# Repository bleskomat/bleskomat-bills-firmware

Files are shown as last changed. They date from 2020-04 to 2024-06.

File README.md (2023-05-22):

# bleskomat-bills-firmware

The Bleskomat Bills ATM is an offline Bitcoin Lightning Network ATM which accepts fiat bank notes and pays-out bitcoin. It's a great educational tool to give others a practical first experience with Bitcoin's Lightning Network.

You can buy the [Bleskomat Bills ATM](https://shop.bleskomat.com/product/bleskomat-bills-atm/) from the official Bleskomat shop. Alternatively, you can find all the components and equipment needed and build your own.

The Bleskomat Bills ATM must be paired with a server to facilitate Lightning Network payments on its behalf; see the options below:
* [Bleskomat Platform](https://platform.bleskomat.com) - non-custodial, requires a monthly subscription
* [bleskomat-server](https://github.com/bleskomat/bleskomat-server) - non-custodial, open-source, self-hosted solution
* [lnbits](https://github.com/lnbits/lnbits-legend) via the Bleskomat extension - open-source, self-hosted and possible to use custodial instances hosted by others; public instances of lnbits:
	* [legend.lnbits.com](https://legend.lnbits.com) - unstable, don't leave funds on this instance for very long

The rest of this document details the hardware and software requirements, how to build the hardware yourself, and instructions for compiling and uploading the firmware from source.

* [Requirements](#requirements)
	* [Hardware Requirements](#hardware-requirements)
	* [Software Requirements](#software-requirements)
* [Building the Hardware Device](#building-the-hardware-device)
	* [Prepare the breadboards](#prepare-the-breadboards)
		* [ESP32 devkit pinout](#esp32-devkit-pinout)
	* [Wiring the Power Supply](#wiring-the-power-supply)
		* [Optionally power the ESP32 devkit via 5V pin](#optionally-power-the-esp32-devkit-via-5v-pin)
	* [Wiring the E-Paper Module](#wiring-the-e-paper-module)
	* [Wiring the Button](#wiring-the-button)
	* [Wiring the Bill Acceptor](#wiring-the-bill-acceptor)
* [Installing Libraries and Dependencies](#installing-libraries-and-dependencies)
* [Compiling and Uploading to Device](#compiling-and-uploading-to-device)
* [Generate Font Header Files](#generate-font-header-files)
* [Configure Bill Acceptor](#configure-bill-acceptor)
* [Configuring the Device](#configuring-the-device)
	* [List of Configuration Options](#list-of-configuration-options)
	* [Browser-Based Configuration Tool](#browser-based-configuration-tool)
	* [Command-Line Configuration Tool](#command-line-configuration-tool)
	* [Hard-Coded Configuration](#hard-coded-configuration)
* [Changelog](#changelog)
* [Support](#support)
* [License](#license)
* [Trademark](#trademark)

## Requirements

This section includes information about the software and hardware requirements needed to build this project.

### Hardware Requirements

The following list includes all the parts needed to build the commercial Bleskomat ATM. The list includes direct links to suppliers of each part.

Basic components/equipment needed to build your own Bleskomat Bills ATM:
* 2 x breadboard (400-pin)
* Jumper wires (M-M)
* Jumper wires (M-F)
* ESP32 Devkit
* NV10 Bill Acceptor from Innovative Technologies
* WaveShare 4.2 inch E-Paper Module (b/w)
* Button
* 10k ohm resistor
* DC 5.5/2.1 mm DIP adapter
* 12V DC power adaptor (1.5A < 3A)
* Standard USB to micro USB cable

Optional components/equipment:
* Soldering iron
* 2.54 mm pins
* To power the ESP32 devkit from the 12V DC power supply:
	* XL4005 step-down converter
	* USB (F) adapter
	* Alternatively, you could use a USB car charger which includes both a step-down converter and USB (F) output

### Software Requirements

* [make](https://www.gnu.org/software/make/)
* [PlatformIO Core (CLI)](https://docs.platformio.org/en/latest/core/)
	* Version 6 or newer
	* Only the CLI ("Core") is required

## Building the Hardware Device

Before proceeding, be sure that you have all the project's [hardware requirements](#hardware-requirements).

### Prepare the breadboards

One breadboard is not large enough to accommodate all the pins of the ESP32 devkit due to the width of the devkit. This is why we recommend to connect two breadboards together.

Remove one of the power rails from one of the breadboards. Use the notches on the sides of the breadboards to connect them together length-wise.

Insert the ESP32 devkit into the pin holes of the new, combined breadboard.

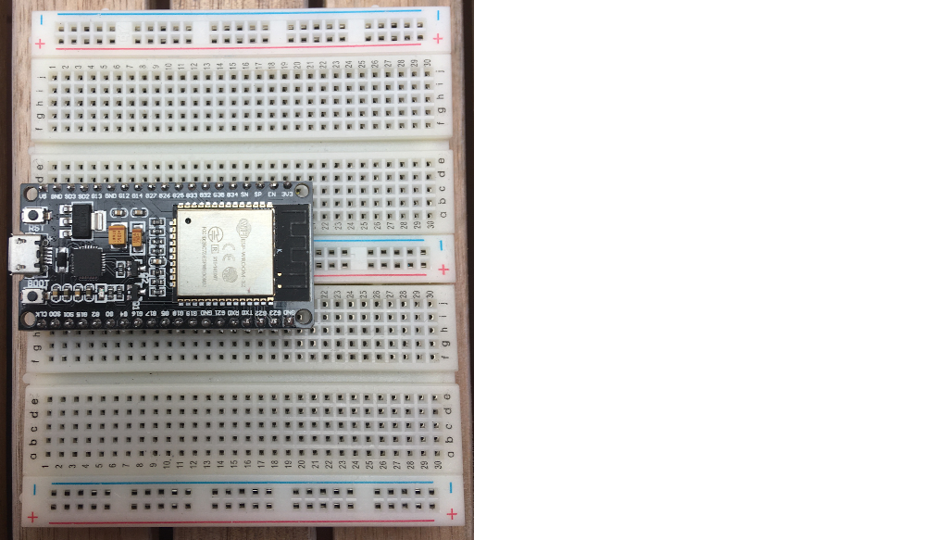
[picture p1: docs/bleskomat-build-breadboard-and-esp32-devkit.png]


Familiarize yourself with the ESP32 devkit's pinout reference below.

#### ESP32 devkit pinout

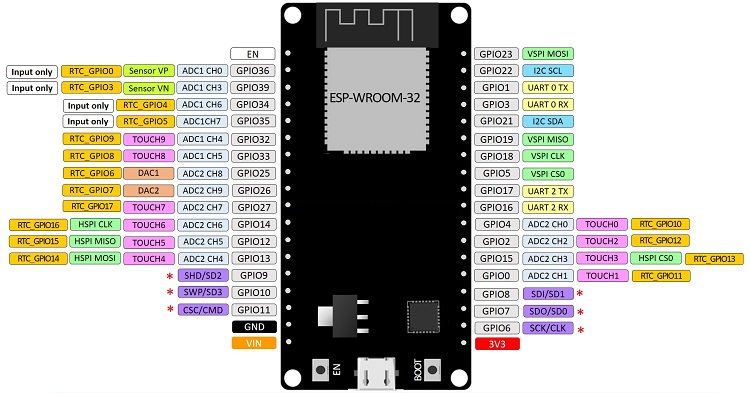
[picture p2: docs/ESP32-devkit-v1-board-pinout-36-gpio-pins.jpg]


### Wiring the Power Supply

The first step to building the device is wiring the power supply. If already plugged in, __unplug__ the 12V DC power supply now. Connect the DC 5.5/2.1 end of the power supply to the DIP adapter. The positive (+) pins should be the power pins and the negative (-) pins should be the ground. You can use your multimeter to check in case you want to be extra safe:
* Plug-in the power supply to electricity
* Turn on your multimeter and set it to measure voltage in the appropriate range (probably 20V)
* Touch the __red__ lead of your multimeter to one of the positive pins
* Touch the __black__ lead of your multimeter to one of the negative pins
* If you see a negative voltage reading, swap the leads between the two wires
* The pin touched by the __black__ lead is the ground ("GND")
* The pin touched by the __red__ lead is the hot wire ("DC12V")
* Unplug the power supply again

Use a pair of M-F jumper wires to connect the DC 5.5/2.1 DIP adapter to one of the breadboard's power rails. Negative to negative, positive to positive. This rail will be your 12V DC power (positive) and the common ground (negative).

#### Optionally power the ESP32 devkit via 5V pin

If you'd like to make your Bleskomat build a little bit more portable, you can power the ESP32 devkit via its 5V pin. To do this you will need the XL4005 (or equivalent) step-down converter and the USB (F) adapter. Note that powering the ESP32 devkit via its micro USB port requires a regulated voltage of approximately 5V.

It's also possible to use a USB car charger in case you have an extra one lying around.

Connect the step-down converter's input pins to the 12V DC power rail and common ground using (M-F) jumper wires. Use a multimeter to measure the voltage at the out pins. In the case of the XL4005, use a small screwdriver to turn the screw on the little blue box. Turning the screw counter clockwise should lower the voltage, turning it the opposite direction should increase the voltage. Once you have the voltage set to 5V, connect the out pins to the center power rails of the breadboard. This will be your 5V DC power rail.

Use a soldering iron to solder four 2.54 mm pins to the USB (F) DIP adapter. Insert the pins directly into the breadboard wherever you have space available. Using (M-M) jumper wires, connect the negative and positive pins of the USB (F) DIP adapter to the 5V DC power rail.

Connect the negative pin of the 5V DC power rail to the negative of the 12V DC power rail to ensure that they share a common ground. This is important because without a common ground shared between the coin acceptor and ESP32 devkit, the ESP32 will not receive a clean signal from the coin acceptor.

Use a standard USB to micro USB cable to connect the USB (F) DIP adapter to the ESP32 devkit.

There are other options when powering the ESP32 - e.g via the 3.3V pin or the 5V/VIN pin. You should __never__ power the ESP32 via more than one of these options at the same time. For example, do not power the ESP32 via its 3.3V pin while also connecting the ESP32 via USB to your computer. This can damage the ESP32 and possibly also your computer.

### Wiring the E-Paper Module

Connect the E-Paper display module to the ESP32 using the following table as a guide:

| ESP32 | E-Paper Display Module |
|---|---|
| D25 | BUSY |
| D26 | RST |
| D27 | DC |
| D15 | CS |
| D13 | CLK |
| D14 | DIN |
| GND | GND |
| 3.3V  | VCC |

Refer to the [ESP32 devkit pinout](#esp32-devkit-pinout) for help identifying the pins on your ESP32.

### Wiring the Button

Insert button pins into the breadboard wherever you have space available. Typically, its best to place the button at the center of a breadboard (over the gap).

Connect the button using the following table as a guide:

| ESP32 | Button |
|---|---|
| VIN (V5) | left pin  |
| GPIO33 | right pin |

Connect the right pin of the button to GND with a 10k ohm resistor.

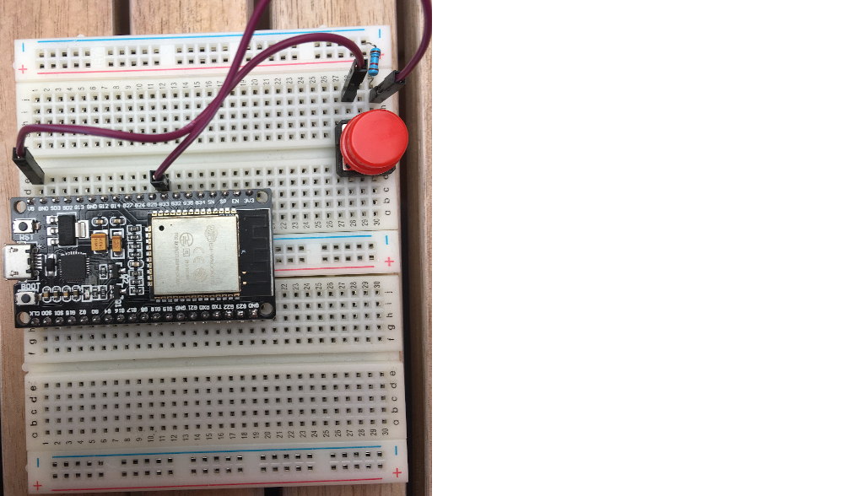
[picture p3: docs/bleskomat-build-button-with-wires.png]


Refer to the [ESP32 devkit pinout](#esp32-devkit-pinout) for help identifying the pins on your ESP32.

### Wiring the Bill Acceptor

This project supports the NV10 (USB+) and NV9 bill acceptors. The SIO protocol is used to communicate with the bill acceptor unit.

|  ESP32 | NV10/NV9 | Power Supply  |
|---|---|---|
| GPIO16 | 1 (Tx) | |
| GPIO17 | 5 (Rx) | |
| | 16 | - Ground |
| | 15 | + 12V DC |

Refer to the [ESP32 devkit pinout](#esp32-devkit-pinout) for help identifying the pins on your ESP32.

## Installing Libraries and Dependencies

Before proceeding, be sure that you have all the project's [software requirements](#software-requirements).

Use make to install libraries and dependencies for the device firmware:
```bash
make install
```
* The firmware's dependencies are defined in its platformio.ini file located at `./platformio.ini`

If while developing you need to install a new library for the device firmware, use the following as a guide:
```bash
platformio lib install LIBRARY_NAME[@VERSION]
```
You can find PlatformIO's libraries repository [here](https://platformio.org/lib).

## Compiling and Uploading to Device

To compile the firmware (without uploading to a device):
```bash
make compile
```

To compile and upload to your device:
```bash
make upload DEVICE=/dev/ttyUSB0
```
The device path for your operating system might be different. If you receive a "Permission denied" error about `/dev/ttyUSB0` then you will need to set permissions for that file on your system:
```bash
sudo chown $USER:$USER /dev/ttyUSB0
```

To open the serial monitor:
```bash
make monitor DEVICE=/dev/ttyUSB0
```
Again the device path here could be different for your operating system.

## Generate Font Header Files

Each font used to render text on the E-Paper display is loaded from a C-style header file. If you need to add another font, expand the character set of an existing font, or add more font sizes; you will need to generate new font header files.

Have otf2bdf utility installed on your system - available via `apt-get` or `apt` on Ubuntu - e.g `apt-get install otf2bdf`.

Manually build bdfconv from source which is included along with this repository:
```sh
make bdfconv
```
Generate fonts:
```sh
make fonts
```
To manually generate fonts:
```sh
./scripts/generate-font-header-files.sh "/path/to/font/file.ttf" 2 32-382 16,20,24,28,32,36,40,44,48
```
* `2` - this is the build mode
	* "Font build mode, 0: proportional, 1: common height, 2: monospace, 3: multiple of 8". Examples:
		* CheckbookLightning = 1
		* Courier Prime Code = 2
* `32-382` - this is the character range (e.g. first character = 32, last = 382). More characters = larger header files.
* `6,7,8,9,10,12,14,16,18,20,22,24,28` - comma-separated list of font sizes

Generated font files are written to the ./include/fonts/u8g2 directory.

## Configure Bill Acceptor

Please refer to the following user manuals for detailed instructions regarding how to configure the NV10 (USB+) bill acceptor:
* [NV10 User Manual](docs/NV10-User-Manual-v1.1.pdf)

## Configuring the Device

It is possible to configure the device via the following methods:
* [Browser-Based Configuration Tool](#browser-based-configuration-tool)
* [Command-Line Configuration Tool](#command-line-configuration-tool)
* [Hard-Coded Configuration](#hard-coded-configuration)

### List of Configuration Options

The following is a list of possible configuration options:
* `apiKey.id` - The API key ID of the device. This is needed by the server to verify signatures created by the device.
* `apiKey.key` - The API key secret that is used to generate signatures.
* `apiKey.encoding` - The explicit encoding of the API key secret. This can be "hex", "base64", or empty-string (e.g "") to mean no encoding. When generating a new API key on the server, it will store the encoding along with the ID and secret.
* `callbackUrl` - The LNURL server base URL plus endpoint path. Example:
	* `https://p.bleskomat.com/u`
* `shorten` - Whether or not to shorten the LNURL; see the [lnurl-node module](https://github.com/chill117/lnurl-node#signed-lnurls) for more details.
* `uriSchemaPrefix` - The URI schema prefix for LNURLs generated by the device. It has been discovered that some wallet apps mistakenly only support lowercase URI schema prefixes. Uppercase is better because when encoded as a QR code, the generated image is less complex and so easier to scan. Set this config to empty-string (e.g `uriSchemaPrefix=`) to not prepend any URI schema prefix.
* `fiatCurrency` - The fiat currency symbol for which the device is configured; see [ISO 4217](https://en.wikipedia.org/wiki/ISO_4217).
* `fiatPrecision` - The number of digits to the right of the decimal point when rendering fiat currency amounts.
* `billValues` - The value of bills for which the bill acceptor has been configured. Each value separated by a comma. Integers and floating point (decimal) values are accepted. Examples:
	* CZK: `100,200,500,1000,2000,5000`
	* EUR: `5,10,20,50,100,200,500`
* `billTxPin` - The GPIO connected to the NV10/NV9's Tx pin.
* `billRxPin` - The GPIO connected to the NV10/NV9's Rx pin.
* `billBaudRate` - The baud rate of the SIO protocol communication with the NV10/NV9. This value will be `300` or `9600`.
* `logLevel` - Possible values:
	* `trace` - everything
	* `debug`
	* `info` - default
	* `warn`
	* `error`
	* `none` - nothing
* `webUrl` - The base URL for the web platform. If non-empty, it will be the base URL for:
	* `/intro?id=API_KEY_ID` - URL shown as a QR code on the instructions screen.
* `platformSockUri` - If the device is connected to WiFi and this value is non-empty, a WebSocket connection will be created to the provided URI. Example values:
	* `wss://platform.bleskomat.com/device` -  Uses TLS encryption, must provide the intermediate CA certificate. This can be saved to the device's SPIFFS file system via the [/serial](https://platform.bleskomat.com/serial) tool.
	* `ws://platform.bleskomat.com/device` - Unencrypted WebSocket
* `platformCACert` - The PEM-encoded CA certificate for the platform. This is used to create a secure (TLS) connection to the platform.
* `onlineOnly` - If set to `1` or `true`, then the ATM will only be enabled when connected to the platform.

### Browser-Based Configuration Tool

The Bleskomat Platform provides a [browser-based configuration tool](https://platform.bleskomat.com/serial) to upload pre-built device firmware, view real-time log output, update device configurations, run JSON-RPC serial commands, and more.

### Command-Line Configuration Tool

It is also possible to use the [bleskomat-cli](https://github.com/bleskomat/bleskomat-cli) command-line utility to communicate with a Bleskomat hardware device via JSON-RPC over serial API. Please refer to that project's readme for installation and usage information.

### Hard-Coded Configuration

Hard-coded configurations can be set by modifying the source file [config.cpp](https://github.com/bleskomat/bleskomat-bills-firmware/blob/master/src/config.cpp#L201).

Each time you make changes to the hard-coded configurations, you will need to re-compile and flash the ESP32's firmware.

## Changelog

See [CHANGELOG.md](https://github.com/bleskomat/bleskomat-bills-firmware/blob/master/CHANGELOG.md)

## Support

Need some help? Join us in the official [Telegram group](https://t.me/bleskomat) or send us an email at [support@bleskomat.com](mailto:support@bleskomat.com) and we will try our best to respond in a reasonable time. If you have a feature request or bug to report, please [open an issue](https://github.com/bleskomat/bleskomat-bills-firmware/issues) in this project repository.

## License

The project is licensed under the [GNU General Public License v3 (GPL-3)](https://tldrlegal.com/license/gnu-general-public-license-v3-(gpl-3)):
> You may copy, distribute and modify the software as long as you track changes/dates in source files. Any modifications to or software including (via compiler) GPL-licensed code must also be made available under the GPL along with build & install instructions.

## Trademark

"Bleskomat" is a registered trademark. You are welcome to hack, fork, build, and use the source code and instructions found in this repository. However, the right to use the name "Bleskomat" with any commercial products or services is withheld and reserved for the trademark owner.

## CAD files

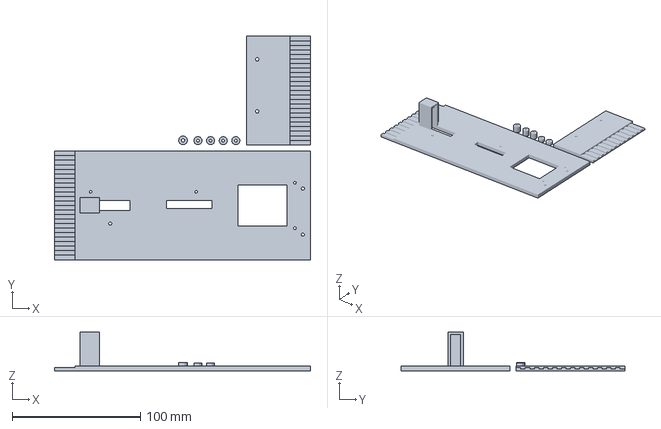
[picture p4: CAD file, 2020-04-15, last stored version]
3d-models/dell-pc-case/dell-pc-case--all.3mf
199.9 x 174.6 x 30.3 mm

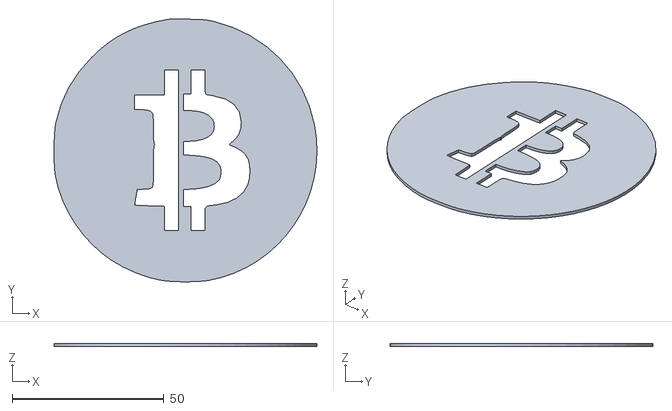
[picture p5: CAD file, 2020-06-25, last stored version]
assets/stencils/bitcoin-lightning/symbol.svg_1mm.stl
86.7 x 86.6 x 1.00

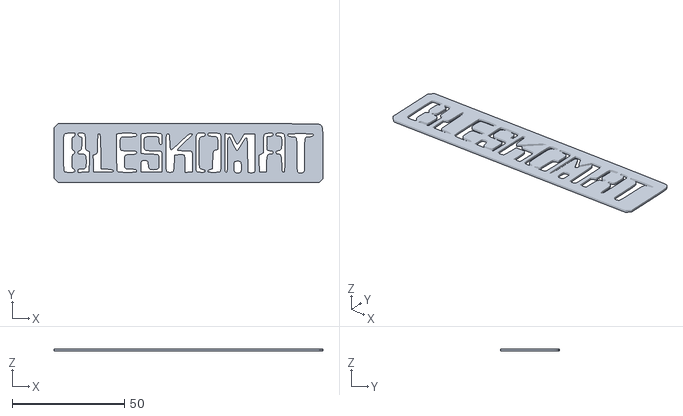
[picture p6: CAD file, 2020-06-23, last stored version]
assets/stencils/logo/stencil-120mm.svg_1mm.stl
120.0 x 26.3 x 1.00

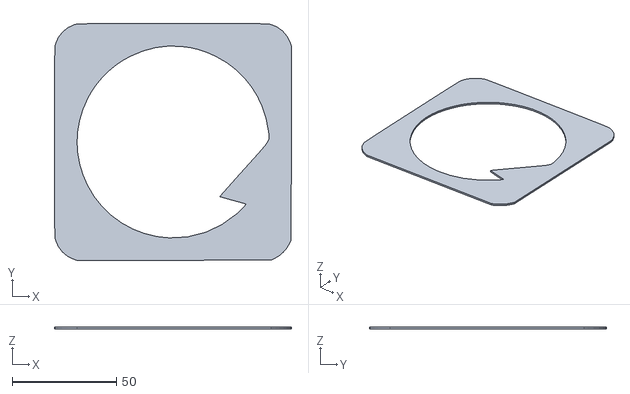
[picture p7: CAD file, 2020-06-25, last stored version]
assets/stencils/bitcoin-lightning/coin.svg_1mm.stl
113.9 x 113.9 x 1.00

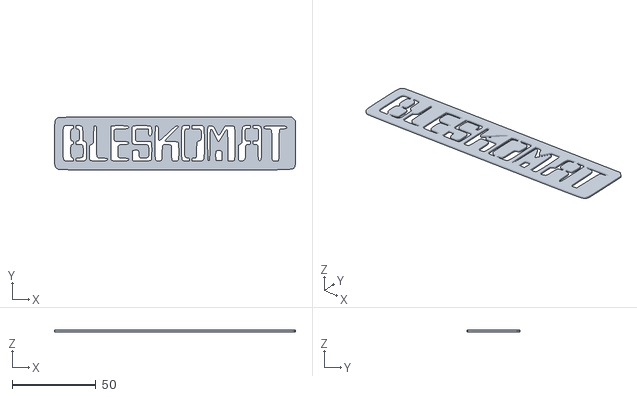
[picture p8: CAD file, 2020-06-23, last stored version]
assets/stencils/logo/stencil-144mm.svg_1mm.stl
143.5 x 31.5 x 1.00

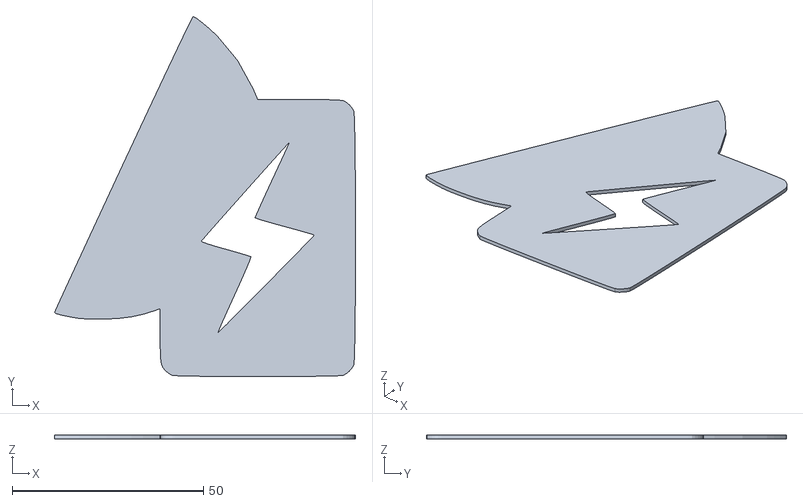
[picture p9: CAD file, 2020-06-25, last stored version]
assets/stencils/bitcoin-lightning/lightning.svg_1mm.stl
78.7 x 94.1 x 1.00

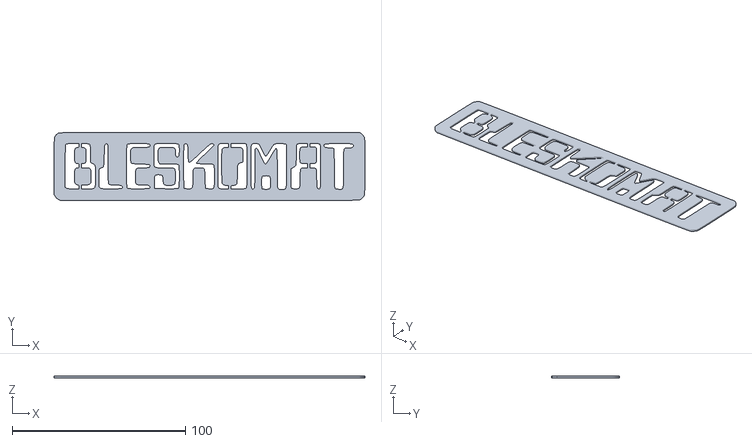
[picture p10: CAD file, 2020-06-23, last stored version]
assets/stencils/logo/stencil-180mm.svg_1mm.stl
179.5 x 39.3 x 1.00

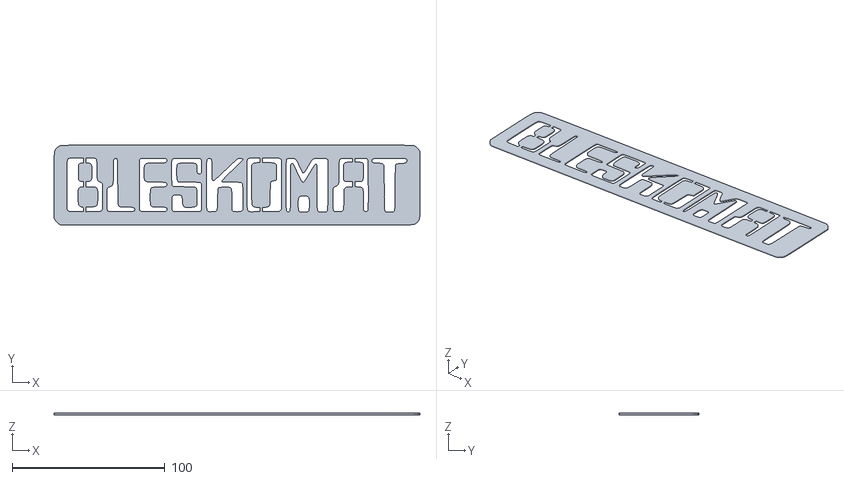
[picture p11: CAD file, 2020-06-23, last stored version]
assets/stencils/logo/stencil-240mm.svg_1mm.stl
240.0 x 52.5 x 1.00

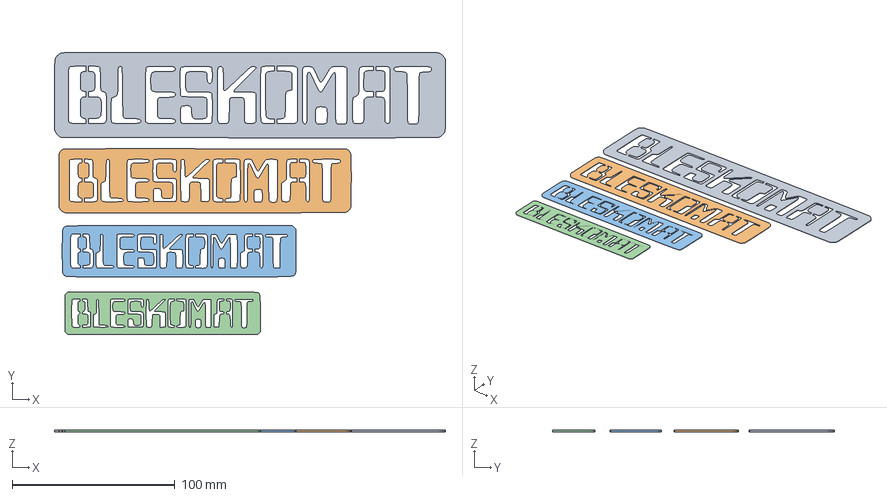
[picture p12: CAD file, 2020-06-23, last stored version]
assets/stencils/logo/stencil-120-240mm.svg_1mm.3mf
240.0 x 173.3 x 1.00 mm
stencil-240mm.svg_1mm.stl
stencil-180mm.svg_1mm.stl
stencil-144mm.svg_1mm.stl
stencil-120mm.svg_1mm.stl

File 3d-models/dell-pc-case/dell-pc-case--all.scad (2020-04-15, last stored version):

spaceBetweenPrintedParts=5;

plateWidth=84.8;
plateHeight=250;
plateThickness=4;

screwTypeOneDiameter=3;
screwTypeOneRadius=screwTypeOneDiameter / 2;
screwTypeTwoDiameter=2.5;
screwTypeTwoRadius=screwTypeTwoDiameter / 2;

// Mounts for parts (e.g screen and coin acceptor):
partMountWallThickness=2;
screenMountHeight=3.2;
coinAcceptorLeftMountHeight=6.1;
coinAcceptorRightMountHeight=6.4;

screwTopSpaceBetween=33;
screwTopLeftPosX=24.7 + screwTypeOneRadius;
screwTopLeftPosY=4.45 + screwTypeOneRadius;
screwTopRightPosX=screwTopLeftPosX + screwTypeOneRadius + screwTopSpaceBetween + screwTypeOneRadius;
screwTopRightPosY=screwTopLeftPosY;

screenMarginTop=10;
screenWidth=32;
screenHeight=38.35;
screenPosX=(plateWidth - screenWidth) / 2;
screenPosY=screwTopLeftPosY + screwTypeTwoDiameter + screenMarginTop;
screenScrewTopLeftPosX=(0.5 + screwTypeTwoRadius) * -1;
screenScrewTopLeftPosY=(5 + screwTypeTwoRadius) * -1;
screenScrewTopRightPosX=screenWidth + 0.5 + screwTypeTwoRadius;
screenScrewTopRightPosY=screenScrewTopLeftPosY;
screenMarginBottom=16;

coinAcceptorMarginTop=4;
coinInsertOutputGap=28.5;
coinOutputWidth=8.1;
coinOutputHeight=36.8;
coinOutputPosX=(plateWidth - coinOutputWidth) / 2;

coinInsertWidth=6.45;
coinInsertHeight=35.85;
coinInsertPosX=coinOutputPosX;
coinInsertPosY=screenPosY + screenHeight + screenMarginBottom + coinAcceptorMarginTop;
coinOutputPosY=coinInsertPosY + coinInsertHeight + coinInsertOutputGap;
coinOutputMarginBottom=22;

toothWidth=plateWidth / floor(plateWidth / 3.5);
toothHeight=16;
topPlateHeight=coinOutputHeight + coinOutputPosY + coinOutputMarginBottom;
topPlatePosX=0;
topPlatePosY=0;
topPlateTeethPosX=topPlatePosX;
topPlateTeethPosY=(topPlatePosY + topPlateHeight) - toothHeight;

bottomPlateHeight=plateHeight - topPlateHeight;
bottomPlatePosX=topPlatePosX + plateWidth + spaceBetweenPrintedParts;
bottomPlatePosY=topPlatePosY;
bottomPlateTeethPosX=0;
bottomPlateTeethPosY=0;

screwBottomSpaceBetween=36.2;
screwBottomLeftPosX=24.65 + screwTypeOneRadius;
screwBottomLeftPosY=bottomPlateHeight - (screwTypeOneDiameter + screwTypeOneRadius + 3.9);
screwBottomRightPosX=screwBottomLeftPosX + screwTypeOneDiameter + screwBottomSpaceBetween + screwTypeOneRadius;
screwBottomRightPosY=screwBottomLeftPosY;

coinAcceptorScrewTopPosX=(7.85 + screwTypeTwoRadius) * -1;
coinAcceptorScrewTopPosY=11.25 + screwTypeTwoRadius;
coinAcceptorScrewBottomPosX=(7.85 + screwTypeTwoRadius) * -1;
coinAcceptorScrewBottomPosY=coinOutputHeight - (5 + screwTypeTwoRadius);
coinAcceptorScrewRightPosX=(14 + screwTypeTwoRadius);
coinAcceptorScrewRightPosY=14 + screwTypeTwoRadius;

maxExpectedCoinDiameter=26.3;
maxExpectedCoinRadius=maxExpectedCoinDiameter / 2;
coinCatchWallThickness=2;
coinCatchWidth=coinOutputWidth + (coinCatchWallThickness * 2);
coinCatchHeight=maxExpectedCoinRadius + coinCatchWallThickness;
coinCatchDepth=maxExpectedCoinDiameter + coinCatchWallThickness;
coinCatchPosX=coinOutputPosX - coinCatchWallThickness;
coinCatchPosY=(coinOutputPosY + coinOutputHeight + coinCatchWallThickness) - coinCatchHeight;
coinCatchPosZ=plateThickness + (coinCatchWallThickness * -1);

// plate (top)
translate([topPlatePosX, topPlatePosY]) {
    union() {
        difference() {
            // plate
            cube([
                plateWidth,
                topPlateHeight,
                plateThickness
            ]);
            // screw (top-left)
            translate([
                // Invert x-coordinate:
                plateWidth - (screwTopLeftPosX + screwTypeOneDiameter),
                screwTopLeftPosY
            ]) {
                cylinder(
                    h=plateThickness,
                    r=screwTypeOneRadius
                );
            }
            // screw (top-right)
            translate([
                plateWidth - (screwTopRightPosX + screwTypeOneDiameter),
                screwTopRightPosY
            ]) {
                cylinder(
                    h=plateThickness,
                    r=screwTypeOneRadius
                );
            }
            // screen
            translate([screenPosX, screenPosY]) {
                cube([
                    screenWidth,
                    screenHeight,
                    plateThickness
                ]);
                // screen screw (top-left)
                translate([
                    screenScrewTopLeftPosX,
                    screenScrewTopLeftPosY
                ]) {
                    cylinder(
                        h=plateThickness,
                        r=screwTypeTwoRadius
                    );
                }
                // screen screw (top-right)
                translate([
                    screenScrewTopRightPosX,
                    screenScrewTopRightPosY
                ]) {
                    cylinder(
                        h=plateThickness,
                        r=screwTypeTwoRadius
                    );
                }
            }
            // coin insert
            translate([
                // Invert x-coordinate:
                plateWidth - (coinInsertPosX + coinInsertWidth),
                coinInsertPosY
            ]) {
                cube([
                    coinInsertWidth,
                    coinInsertHeight,
                    plateThickness
                ]);
                // screw (top)
                translate([
                    // Invert x-coordinate:
                    coinInsertWidth - (coinAcceptorScrewTopPosX + screwTypeTwoDiameter),
                    coinAcceptorScrewTopPosY
                ]) {
                    cylinder(
                        h=plateThickness,
                        r=screwTypeTwoRadius
                    );
                }
            }
            // coin output
            translate([coinOutputPosX, coinOutputPosY]) {
                cube([
                    coinOutputWidth,
                    coinOutputHeight,
                    plateThickness
                ]);
                // screw (bottom)
                translate([
                    // Invert x-coordinate:
                    coinOutputWidth - (coinAcceptorScrewBottomPosX + screwTypeTwoDiameter),
                    coinAcceptorScrewBottomPosY
                ]) {
                    cylinder(
                        h=plateThickness,
                        r=screwTypeTwoRadius
                    );
                }
                // screw (right)
                translate([
                    // Invert x-coordinate:
                    coinOutputWidth - (coinAcceptorScrewRightPosX + screwTypeOneDiameter),
                    coinAcceptorScrewRightPosY
                ]) {
                    cylinder(
                        h=plateThickness,
                        r=screwTypeOneRadius
                    );
                }
            }
            // teeth
            translate([
                topPlateTeethPosX,
                topPlateTeethPosY,
                plateThickness * (2/3)
            ]) {
                cube([
                    plateWidth,
                    toothHeight,
                    (plateThickness / 3) + 0.1
                ]);
                translate([0, 0, plateThickness / -3]) {
                    for (offsetX=[toothWidth : toothWidth * 2 : plateWidth]) {
                        translate([offsetX, 0]) {
                            cube([
                                toothWidth,
                                toothHeight,
                                (plateThickness / 3) + 0.1
                            ]);
                        }
                    }
                }
            }
        }
        // coin output catch
        difference() {
            translate([
                coinCatchPosX,
                coinCatchPosY,
                coinCatchPosZ
            ]) {
                cube([
                    coinCatchWidth,
                    coinCatchHeight,
                    coinCatchDepth
                ]);
            }
            translate([
                coinCatchPosX + coinCatchWallThickness,
                coinCatchPosY - coinCatchWallThickness,
                coinCatchPosZ - coinCatchWallThickness
            ]) {
                cube([
                    coinCatchWidth - (coinCatchWallThickness * 2),
                    coinCatchHeight,
                    coinCatchDepth
                ]);
            }
        }
    }
}
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

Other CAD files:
3d-models/case/bleskomat-prototype-case-v1.dxf
assets/case/bleskomat-prototype-case-v1.dxf
3d-models/dell-pc-case/dell-pc-case--all.stl
assets/dell-pc-case/dell-pc-case--all.stl

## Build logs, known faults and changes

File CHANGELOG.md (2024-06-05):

# Changelog

* v1.6.1:
	* Fix JSON-RPC getconfig when called with empty array should return all configurations
* v1.6.0:
	* Bluetooth JSON-RPC interface enabled when button pressed at boot
	* Wait for JSON-RPC serial interface to time-out before initializing e-paper, bill acceptor
* v1.5.0:
	* Update splash screen
	* Ping, reconnect to NV10 bill acceptor via serial
	* Fixup font rendering
	* Fix locale strings
	* Remove SD card related code
	* Cache state to be restored when device restarts in case of a crash, power loss, etc.
	* Add hardware build instructions
* v1.3.4:
	* Better initialization state handling
* v1.3.3:
	* Fix getInt/Short/Float config value when set to empty-string
* v1.3.2:
	* Added spiffsFormatted config flag
	* Return spiffsInitialized flag in getinfo JSON-RPC command
	* Send response for restart JSON-RPC command
* v1.3.1:
	* Fix randomly failing platform WebSocket connection
* v1.3.0:
	* Added "onlineOnly" configuration option
	* Fixed TLS connection problems
		* "platformCACert" configuration option can contain the CA cert for TLS
	* Improved logging
	* Simplify network/platform.cpp and SD card usage
	* Use SPIFFS file system to store logs
	* JSON-RPC via serial - echo, getconfig, setconfig, getlogs, deletelogs, spiffs_reformat, restart
	* Button delay to fix issue re: accidental clearing of QR code
	* Move bill/coin/button build flags to configuration options
	* Fix excessive memory usage (RAM) by i18n/locale
* v1.2.0:
	* Tagged release version

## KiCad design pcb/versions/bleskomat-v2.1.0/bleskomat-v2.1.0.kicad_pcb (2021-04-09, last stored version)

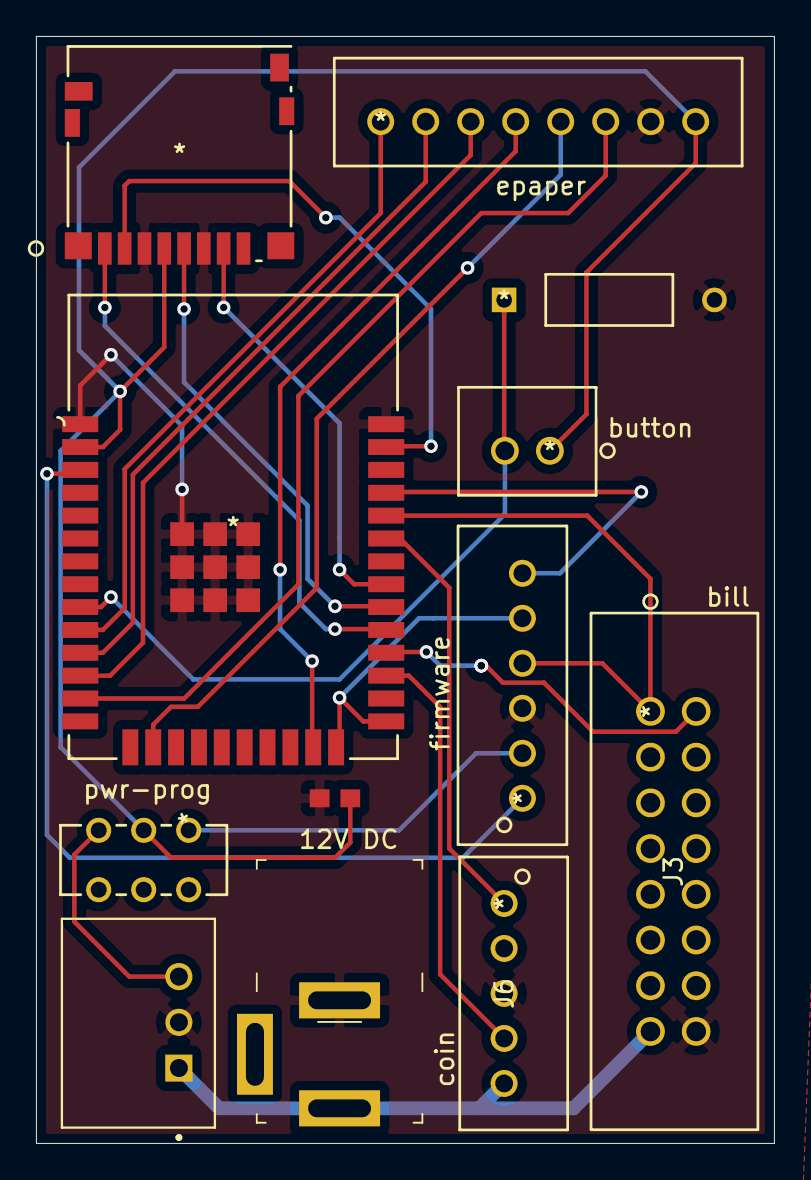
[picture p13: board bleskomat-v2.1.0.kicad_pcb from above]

Board: 2 copper layers, 41.0 x 61.5 mm, 12 parts (0 on the bottom side), 23 nets.

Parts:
12V DC: 12V-SOCKET; Barrel_Jack_5.5mmODx2.1mmID_PJ-202A
D1: LED-LTST-C194TBKT; 0603
J1: firmware; B6B-XH-ALFSN
J2: epaper; B8B-XH-A LFSN
J3: bill; 30316-6002HB
J4: button; B2B-XH-ALFSN
J5: SD_CARD; DM3D-SF
J6: coin; B5B-XH-A LFSN
PS1: step-down-R-78E3.3-1.0; CONV_R-78E3.3-1.0
R1: R 10K; CFR-25JB-52-10K
U1: ESP32-WROOM-32_8MB; ESP32-WROOM-32 8MB
U2: switch power JS202011CQN; JS202011CQN

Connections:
GND: 12V DC.2, D1.1, J1.3, J2.7, J3.16, J5.3, J5.6, J6.3, PS1.2, R1.2, U1.1, U1.38, U1.39, U1.40, U1.41, U1.42, U1.43, U1.44, U1.45, U1.46, U1.47
unnamed: D1.2, J2.8, J4.1, J5.4, U1.2, U2.2
unnamed: J1.1, U1.3
unnamed: J1.2, U2.1
unnamed: J1.4, J3.1, U1.34
unnamed: J1.5, U1.24, U1.25
unnamed: J1.6, U1.35
unnamed: J2.1, U1.10
unnamed: J2.2, U1.11
unnamed: J2.3, U1.12
unnamed: J2.4, U1.23
unnamed: J2.5, U1.16
unnamed: J2.6, U1.13
unnamed: J3.2, U1.28
unnamed: 12V DC.1, J3.15, J6.5, PS1.1
unnamed: J4.2, R1.1, U1.9
unnamed: J5.1, U1.29
unnamed: J5.2, U1.37
unnamed: J5.5, U1.30
unnamed: J5.7, U1.31
unnamed: J6.1, U1.33
unnamed: J6.4, U1.27
unnamed: PS1.3, U2.3

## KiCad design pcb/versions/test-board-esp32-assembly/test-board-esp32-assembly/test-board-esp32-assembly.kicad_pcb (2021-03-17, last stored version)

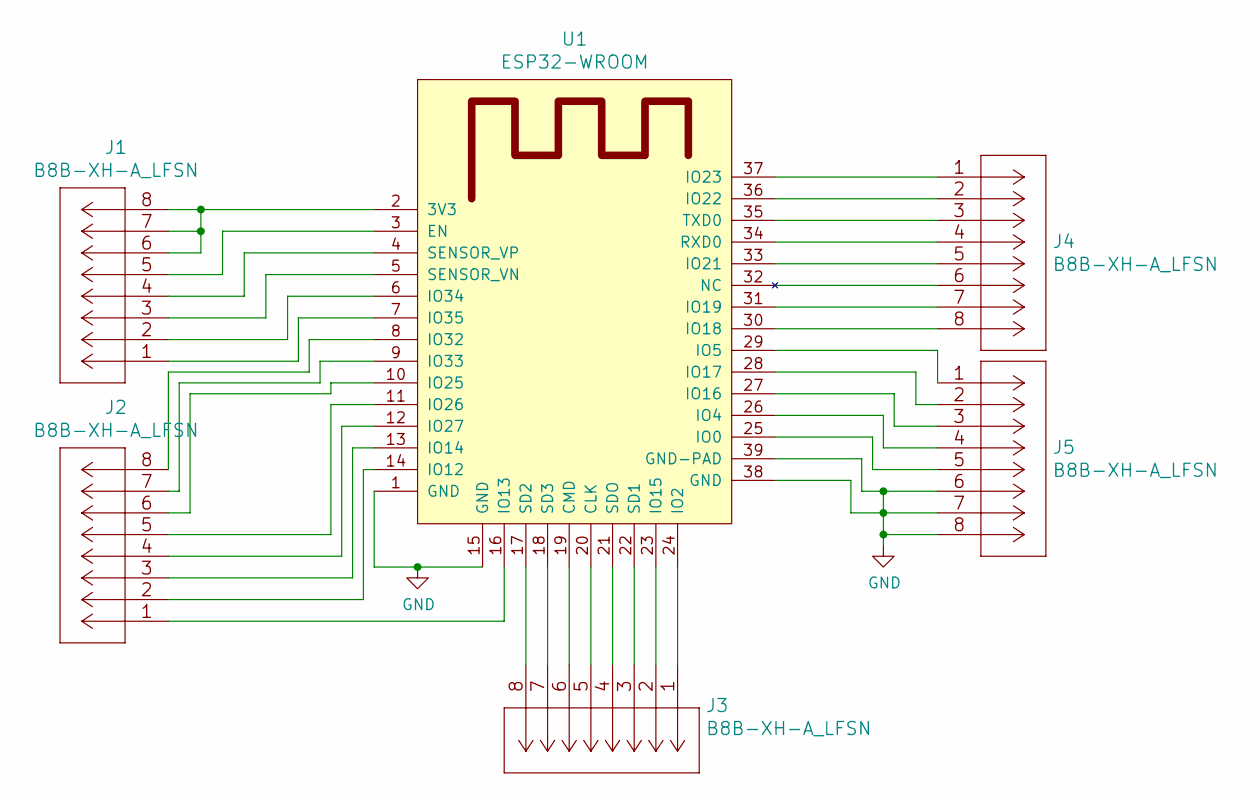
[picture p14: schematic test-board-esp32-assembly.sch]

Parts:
J1, J2, J3, J4, J5: B8B-XH-A_LFSN; B8B-XH-A LFSN
U1: ESP32-WROOM

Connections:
GND: J5.6, J5.7, J5.8, U1.1 (GND), U1.15 (GND), U1.38 (GND), U1.39 (GND-PAD)
unnamed: J1.1, U1.7 (IO35)
unnamed: J1.2, U1.6 (IO34)
unnamed: J1.3, U1.5 (SENSOR_VN)
unnamed: J1.4, U1.4 (SENSOR_VP)
unnamed: J1.5, U1.3 (EN)
unnamed: J1.6, J1.7, J1.8, U1.2 (3V3)
unnamed: J2.1, U1.16 (IO13)
unnamed: J2.2, U1.14 (IO12)
unnamed: J2.3, U1.13 (IO14)
unnamed: J2.4, U1.12 (IO27)
unnamed: J2.5, U1.11 (IO26)
unnamed: J2.6, U1.10 (IO25)
unnamed: J2.7, U1.9 (IO33)
unnamed: J2.8, U1.8 (IO32)
unnamed: J3.1, U1.24 (IO2)
unnamed: J3.2, U1.23 (IO15)
unnamed: J3.3, U1.22 (SD1)
unnamed: J3.4, U1.21 (SDO)
unnamed: J3.5, U1.20 (CLK)
unnamed: J3.6, U1.19 (CMD)
unnamed: J3.7, U1.18 (SD3)
unnamed: J3.8, U1.17 (SD2)
unnamed: J4.1, U1.37 (IO23)
unnamed: J4.2, U1.36 (IO22)
unnamed: J4.3, U1.35 (TXD0)
unnamed: J4.4, U1.34 (RXD0)
unnamed: J4.5, U1.33 (IO21)
unnamed: J4.6, U1.32 (NC)
unnamed: J4.7, U1.31 (IO19)
unnamed: J4.8, U1.30 (IO18)
unnamed: J5.1, U1.29 (IO5)
unnamed: J5.2, U1.28 (IO17)
unnamed: J5.3, U1.27 (IO16)
unnamed: J5.4, U1.26 (IO4)
unnamed: J5.5, U1.25 (IO0)

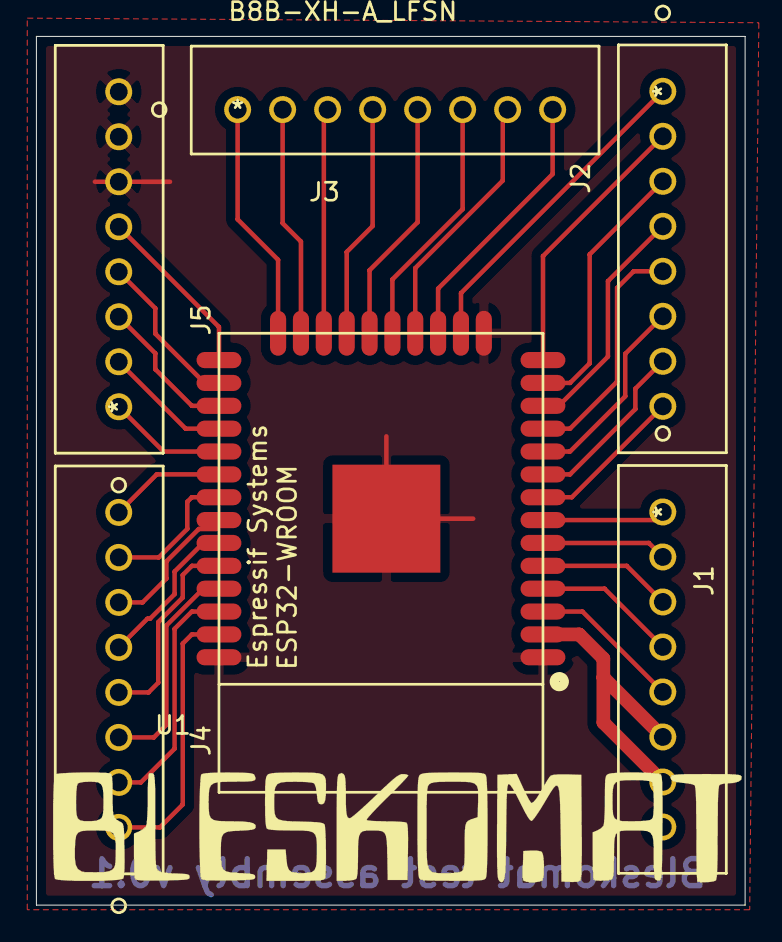
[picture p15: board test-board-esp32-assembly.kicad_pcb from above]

Board: 2 copper layers, 39.4 x 48.3 mm, 6 parts (0 on the bottom side), 36 nets.

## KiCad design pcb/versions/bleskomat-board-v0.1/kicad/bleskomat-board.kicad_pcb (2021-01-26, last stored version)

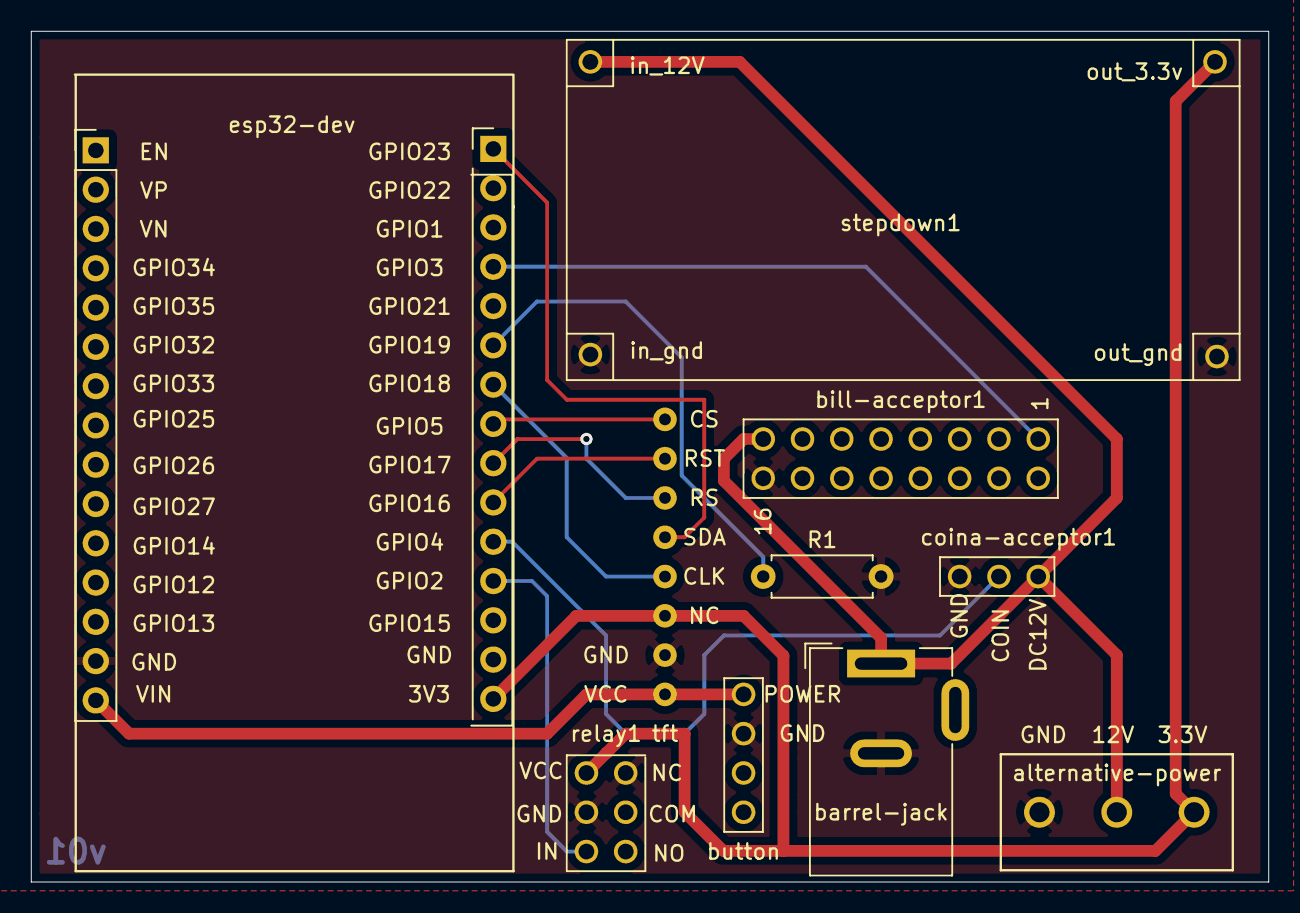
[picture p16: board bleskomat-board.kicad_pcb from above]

Board: 2 copper layers, 80.0 x 55.0 mm, 10 parts (0 on the bottom side), 13 nets.

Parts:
R1: 10k; R_Axial_DIN0207_L6.3mm_D2.5mm_P7.62mm_Horizontal
alternative-power: Screw_Terminal_01x03; TerminalBlock_5mm
barrel-jack: 12V-SOCKET; BarrelJack_Wuerth_6941xx301002
bill-acceptor1: billacceptor-connector
button: button; button-connector
coina-acceptor1: coinacceptor-connector
esp32-dev: esp32; ESP32_Devkit_DOIT_V2
relay1: relay-connector; relay-temporary-connector
stepdown1: stepdown-connector; stepdown
tft: tft-connector

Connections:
GND: R1.2, alternative-power.1, barrel-jack.2, bill-acceptor1.16, button.2, coina-acceptor1.3, esp32-dev.14, relay1.3, relay1.5, stepdown1.1, stepdown1.3, tft.7
unnamed: alternative-power.2, barrel-jack.1, bill-acceptor1.15, coina-acceptor1.1, stepdown1.2
unnamed: alternative-power.3, esp32-dev.16, relay1.6, stepdown1.4, tft.6
unnamed: R1.1, esp32-dev.25
unnamed: button.1, esp32-dev.15, tft.8
unnamed: esp32-dev.19, relay1.4
unnamed: coina-acceptor1.2, esp32-dev.20
unnamed: esp32-dev.21, tft.2
unnamed: esp32-dev.22, tft.3
unnamed: esp32-dev.23, tft.1
unnamed: esp32-dev.24, tft.5
unnamed: bill-acceptor1.1, esp32-dev.27
unnamed: esp32-dev.30, tft.4

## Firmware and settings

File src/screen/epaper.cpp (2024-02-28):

#include "screen/epaper.h"

//
//  Using GxEPD2 library:
//  	https://github.com/ZinggJM/GxEPD2
//  Which builds on Adafruit-GFX-Library:
//  	https://github.com/adafruit/Adafruit-GFX-Library
//
//  For utf-8 support, the following additional library is used:
//  https://github.com/olikraus/U8g2_for_Adafruit_GFX
//
//  Example usage:
//  https://github.com/ZinggJM/GxEPD2/blob/master/examples/GxEPD2_U8G2_Fonts_Example/GxEPD2_U8G2_Fonts_Example.ino
//

namespace {

	enum class State {
		uninitialized,
		initialized,
		failed
	};
	State state = State::uninitialized;

	GxEPD2_BW<GxEPD2_420, GxEPD2_420::HEIGHT> display(GxEPD2_420(EPAPER_CS, EPAPER_DC, EPAPER_RST, EPAPER_BUSY));
	U8G2_FOR_ADAFRUIT_GFX u8g2Fonts;

	struct BoundingBox {
		int16_t x = 0;
		int16_t y = 0;
		uint16_t w = 0;
		uint16_t h = 0;
	};

	BoundingBox renderedAmountTextBoundingBox;

	const auto backgroundColor = GxEPD_WHITE;
	const auto textColor = GxEPD_BLACK;

	typedef const uint8_t* Font;
	typedef std::vector<Font> FontList;

	FontList monospaceFonts = {
		// Ordered from largest (top) to smallest (bottom).
		u8g2_courier_prime_code_48pt,
		u8g2_courier_prime_code_44pt,
		u8g2_courier_prime_code_40pt,
		u8g2_courier_prime_code_36pt,
		u8g2_courier_prime_code_32pt,
		u8g2_courier_prime_code_28pt,
		u8g2_courier_prime_code_24pt,
		u8g2_courier_prime_code_20pt,
		u8g2_courier_prime_code_16pt,
		u8g2_courier_prime_code_14pt,
		u8g2_courier_prime_code_12pt,
		u8g2_courier_prime_code_11pt,
		u8g2_courier_prime_code_9pt,
		u8g2_courier_prime_code_8pt
	};

	FontList brandFonts = {
		// Ordered from largest (top) to smallest (bottom).
		u8g2_checkbooklightning_48pt,
		u8g2_checkbooklightning_44pt,
		u8g2_checkbooklightning_40pt,
		u8g2_checkbooklightning_36pt
	};

	Font monospaceFontSmall = u8g2_courier_prime_code_12pt;
	Font monospaceFontNormal = u8g2_courier_prime_code_16pt;

	std::string currentScreen = "";

	BoundingBox calculateTextSize(const std::string &t_text, const Font font) {
		BoundingBox bbox;
		const char* text = t_text.c_str();
		u8g2Fonts.setFontMode(1);// use u8g2 transparent mode (this is default)
		u8g2Fonts.setFontDirection(0);// left to right (this is default)
		u8g2Fonts.setForegroundColor(textColor);// apply Adafruit GFX color
		u8g2Fonts.setBackgroundColor(backgroundColor);// apply Adafruit GFX color
		u8g2Fonts.setFont(font);
		int16_t tbw = u8g2Fonts.getUTF8Width(text);// text box width
		int16_t ta = u8g2Fonts.getFontAscent();// positive
		int16_t td = u8g2Fonts.getFontDescent();// negative; in mathematicians view
		int16_t tbh = ta - td;// text box height
		bbox.w = tbw;
		bbox.h = tbh;
		return bbox;
	}

	Font getBestFitFont(const std::string &text, const FontList fonts, uint16_t max_w = 0, uint16_t max_h = 0) {
		if (max_w == 0) {
			max_w = display.epd2.WIDTH;
		}
		if (max_h == 0) {
			max_h = display.epd2.HEIGHT;
		}
		for (uint8_t index = 0; index < fonts.size(); index++) {
			const Font font = fonts.at(index);
			const BoundingBox bbox = calculateTextSize(text, font);
			if (bbox.w <= max_w && bbox.h <= max_h) {
				// Best fit font found.
				return font;
			}
		}
		// Default to last font in list - should be smallest.
		return fonts.back();
	}

	std::string getAmountFiatCurrencyString(const float &amount) {
		return util::floatToStringWithPrecision(amount, config::getUnsignedInt("fiatPrecision")) + " " + config::getString("fiatCurrency");
	}

	BoundingBox renderText(
		const std::string &t_text,
		const Font font,
		const int16_t &x,
		const int16_t &y,
		const bool &center = true
	) {
		BoundingBox bbox;
		const char* text = t_text.c_str();
		u8g2Fonts.setFontMode(0);// use u8g2 non-transparent mode
		u8g2Fonts.setFontDirection(0);// left to right (this is default)
		u8g2Fonts.setForegroundColor(textColor);// apply Adafruit GFX color
		u8g2Fonts.setBackgroundColor(backgroundColor);// apply Adafruit GFX color
		u8g2Fonts.setFont(font);
		int16_t tbw = u8g2Fonts.getUTF8Width(text);// text box width
		int16_t ta = u8g2Fonts.getFontAscent();// positive
		int16_t td = u8g2Fonts.getFontDescent();// negative; in mathematicians view
		int16_t tbh = ta - td;// text box height
		int16_t box_x = x;
		int16_t box_y = y;
		int16_t w_adjust = 4;
		int16_t h_adjust = 8;
		tbw += w_adjust;
		tbh += h_adjust;
		if (center) {
			box_x -= (tbw / 2);
			box_y -= (tbh / 2);
		}
		int16_t cursor_x = box_x;
		int16_t cursor_y = box_y + tbh;
		cursor_y -= (h_adjust - 2);
		display.fillRect(box_x, box_y, tbw, tbh, backgroundColor);
		u8g2Fonts.setCursor(cursor_x, cursor_y);
		u8g2Fonts.print(text);
		bbox.x = box_x;
		bbox.y = box_y;
		bbox.w = tbw;
		bbox.h = tbh;
		// Uncomment the following line to print debug info to serial monitor:
		// std::cout << "renderText \"" << t_text << "\" / x, y, w, h: " << +box_x << ", " << +box_y << ", " << +tbw << ", " << +tbh << " " << std::endl;
		// Uncomment the following line to draw the outer bounding box.
		// display.drawRect(box_x, box_y, tbw, tbh, textColor);
		return bbox;
	}

	BoundingBox renderQRCode(
		const std::string &t_data,
		const int16_t &x,
		const int16_t &y,
		const uint16_t &max_w,
		const uint16_t &max_h,
		const bool &center = true
	) {
		BoundingBox bbox;
		try {
			const char* data = t_data.c_str();
			uint8_t version = 1;
			while (version <= 40) {
				const uint16_t bufferSize = qrcode_getBufferSize(version);
				QRCode qrcode;
				uint8_t qrcodeData[bufferSize];
				const int8_t result = qrcode_initText(&qrcode, qrcodeData, version, ECC_LOW, data);
				if (result == 0) {
					// QR encoding successful.
					uint8_t scale = std::min(std::floor(max_w / qrcode.size), std::floor(max_h / qrcode.size));
					uint16_t w = qrcode.size * scale;
					uint16_t h = w;
					int16_t box_x = x;
					int16_t box_y = y;
					if (center) {
						box_x -= (w / 2);
						box_y -= (h / 2);
					}
					display.fillRect(box_x, box_y, w, h, backgroundColor);
					for (uint8_t y = 0; y < qrcode.size; y++) {
						for (uint8_t x = 0; x < qrcode.size; x++) {
							auto color = qrcode_getModule(&qrcode, x, y) ? textColor: backgroundColor;
							display.fillRect(box_x + scale*x, box_y + scale*y, scale, scale, color);
						}
					}
					bbox.x = box_x;
					bbox.y = box_y;
					bbox.w = w;
					bbox.h = h;
					break;
				} else if (result == -2) {
					// Data was too long for the QR code version.
					version++;
				} else if (result == -1) {
					throw std::runtime_error("Render QR code failure: Unable to detect mode");
				} else {
					throw std::runtime_error("Render QR code failure: Unknown failure case");
				}
			}
		} catch (const std::exception &e) {
			std::cerr << e.what() << std::endl;
		}
		return bbox;
	}

	void scrub() {
		// Repeatedly clear the screen w/ alternating colors.
		// This ensures that no pixels are left over from a previous state.
		display.clearScreen((uint8_t) textColor);
		display.clearScreen((uint8_t) backgroundColor);
	}

	uint16_t numWrites = 0;
	bool isDirty(const uint16_t maxWrites = 5) {
		return ++numWrites > maxWrites;
	}

	bool startNewScreen(const uint16_t maxWrites = 5) {
		bool scrubbed = false;
		if (currentScreen == "tradeComplete" || isDirty(maxWrites)) {
			scrub();
			scrubbed = true;
			numWrites = 1;
		}
		display.setFullWindow();
		display.fillScreen(backgroundColor);
		return scrubbed;
	}

	void finishNewScreen(const std::string &name) {
		currentScreen = name;
		display.displayWindow(0, 0, display.epd2.WIDTH, display.epd2.HEIGHT);
	}

	std::string getInstructionsUrl() {
		const std::string apiKeyId = config::getString("apiKey.id");
		std::string instructionsUrl = config::getString("webUrl");
		instructionsUrl += "/intro?id=" + util::urlEncode(apiKeyId);
		return instructionsUrl;
	}

	std::vector<std::string> splitTextIntoWords(const std::string &text) {
		std::vector<std::string> words;
		std::stringstream ss(text);
		std::string word;
		while (std::getline(ss, word, ' ')) {
			words.push_back(word);
		}
		return words;
	}

	std::vector<std::string> splitTextIntoLines(const std::string &text, const uint8_t numLines = 2) {
		std::vector<std::string> lines;
		std::vector<std::string> words = splitTextIntoWords(text);
		const uint16_t maxCharWidth = std::ceil(text.size() / numLines) + 4;
		std::string line;
		for (uint8_t index = 0; index < words.size(); index++) {
			if (line != "") {
				line += " ";
			}
			line += words[index];
			if (lines.size() + 1 < numLines && line.size() + 1 + words[index + 1].size() > maxCharWidth) {
				lines.push_back(line);
				line = "";
			}
		}
		lines.push_back(line);
		return lines;
	}
}

namespace screen_epaper {

	void init() {}

	void loop() {
		if (state == State::uninitialized && !jsonRpc::inUse()) {
			logger::write("Initializing e-paper display...");
			if (display.epd2.panel == GxEPD2::GDEW042T2) {
				try {
					display.init(0);
					u8g2Fonts.begin(display);// connect u8g2 procedures to Adafruit GFX
					// It is necessary to stop other SPI device(s) before initializing SPI for the epaper display.
					SPI.end();
					SPI.begin(EPAPER_CLK, EPAPER_MISO, EPAPER_DIN, EPAPER_CS);
					display.setRotation(0);
					state = State::initialized;
				} catch (const std::exception &e) {
					logger::write("Failed to initialize e-paper display: " + std::string(e.what()), "error");
					state = State::failed;
				}
			} else {
				logger::write("Unknown display connected. This firmware supports WaveShare 4.2 inch e-paper b/w", "warn");
				state = State::failed;
			}
		}
	}

	bool isReady() {
		return state == State::initialized;
	}

	void showSplashScreen() {
		if (!screen_epaper::isReady()) return;
		logger::write("Show screen: Splash");
		startNewScreen();
		const int16_t margin = 20;
		const int16_t center_x = (display.epd2.WIDTH / 2);
		BoundingBox prevText_bbox;
		{
			const std::string text = "BLESKOMAT";
			const Font font = getBestFitFont(text, brandFonts);
			const BoundingBox bbox = calculateTextSize(text, font);
			const int16_t pos_x = center_x;
			const int16_t pos_y = (display.epd2.HEIGHT / 2) - margin;// center
			prevText_bbox = renderText(text, font, pos_x, pos_y);
		}
		{
			const std::string text = i18n::t("Bitcoin Lightning devices made easy.");
			const uint16_t max_w = std::ceil((display.epd2.WIDTH * 4) / 5);
			const Font font = getBestFitFont(text, monospaceFonts, max_w);
			const BoundingBox bbox = calculateTextSize(text, font);
			const int16_t pos_x = center_x;
			const int16_t pos_y = prevText_bbox.y - (bbox.h + (margin / 2));
			renderText(text, font, pos_x, pos_y);
		}
		{
			const std::string text = "(" + i18n::t("press button to begin") + ")";
			const uint16_t max_w = std::ceil((display.epd2.WIDTH * 4) / 5);
			const Font font = getBestFitFont(text, monospaceFonts, max_w);
			const BoundingBox bbox = calculateTextSize(text, font);
			const int16_t pos_x = center_x;
			const int16_t pos_y = display.epd2.HEIGHT - (bbox.h + margin);
			renderText(text, font, pos_x, pos_y);
		}
		finishNewScreen("splash");
	}

	void showDisabledScreen() {
		if (!screen_epaper::isReady()) return;
		logger::write("Show screen: Disabled");
		startNewScreen();
		const int16_t margin = 20;
		const std::string text = i18n::t("Temporarily disabled");
		const int16_t text_x = (display.epd2.WIDTH / 2);// center
		const int16_t text_y = (display.epd2.HEIGHT / 2) - margin;
		const Font font = getBestFitFont(text, monospaceFonts);
		const BoundingBox text_bbox = renderText(text, font, text_x, text_y);
		const std::string text2 = i18n::t("Please check again later");
		const int16_t text2_x = display.epd2.WIDTH / 2;// center
		const int16_t text2_y = text_bbox.h + text_bbox.y + margin;// bottom
		renderText(text2, monospaceFontSmall, text2_x, text2_y);
		finishNewScreen("disabled");
	}

	void showInstructionsScreen() {
		if (!screen_epaper::isReady()) return;
		logger::write("Show screen: Instructions");
		startNewScreen();
		const std::string instructionsUrl = getInstructionsUrl();
		const int16_t margin = 20;
		const int16_t line_spacing = 8;
		BoundingBox qrcode_bbox;
		{
			const uint16_t qrcode_w = 100;
			const uint16_t qrcode_h = 100;
			const int16_t qrcode_x = margin;
			const int16_t qrcode_y = margin;
			qrcode_bbox = renderQRCode(instructionsUrl, qrcode_x, qrcode_y, qrcode_w, qrcode_h, false);
		}
		{
			std::vector<std::string> lines = splitTextIntoLines(i18n::t("Scan this QR code to see a list of supported mobile wallet apps"), 3);
			int16_t line1_x = qrcode_bbox.x + qrcode_bbox.w + margin;// right of the QR code
			int16_t line1_y = qrcode_bbox.y;// align w/ QR code
			const int16_t max_w = display.epd2.WIDTH - (line1_x + margin);
			const Font font = u8g2_courier_prime_code_11pt;
			BoundingBox prevText_bbox;
			prevText_bbox = renderText(lines[0], font, line1_x, line1_y, false);
			int16_t line2_y = prevText_bbox.y + prevText_bbox.h + line_spacing;
			prevText_bbox = renderText(lines[1], font, line1_x, line2_y, false);
			int16_t line3_y = prevText_bbox.y + prevText_bbox.h + line_spacing;
			prevText_bbox = renderText(lines[2], font, line1_x, line3_y, false);
		}
		{
			const int16_t box_margin = line_spacing / 2;
			const int16_t box_x = margin;
			const int16_t box_y = qrcode_bbox.y + qrcode_bbox.h + margin;
			const uint16_t box_w = display.epd2.WIDTH - (margin * 2);
			const uint16_t box_h = display.epd2.HEIGHT - (box_y + margin);
			display.drawRect(box_x, box_y, box_w, box_h, textColor);
			const std::string numbering1 = "0";
			const std::string numbering2 = "1";
			const std::string numbering3 = "2";
			const std::string numbering4 = "3";
			const Font numbering_font = u8g2_courier_prime_code_16pt;
			BoundingBox numbering1_bbox = calculateTextSize(numbering1, numbering_font);
			int16_t numbering1_x = box_x + box_margin + (numbering1_bbox.w / 2);// left, inside box
			int16_t numbering1_y = box_y + box_margin;// top, inside box
			numbering1_bbox = renderText(numbering1, numbering_font, numbering1_x, numbering1_y, false);
			int16_t numbering2_y = numbering1_bbox.y + numbering1_bbox.h + line_spacing;
			BoundingBox numbering2_bbox = renderText(numbering2, numbering_font, numbering1_x, numbering2_y, false);
			int16_t numbering3_y = numbering2_bbox.y + numbering2_bbox.h + line_spacing;
			BoundingBox numbering3_bbox = renderText(numbering3, numbering_font, numbering1_x, numbering3_y, false);
			int16_t numbering4_y = numbering3_bbox.y + numbering3_bbox.h + line_spacing;
			BoundingBox numbering4_bbox = renderText(numbering4, numbering_font, numbering1_x, numbering4_y, false);
			const std::string text4 = i18n::t("Install supported mobile wallet app");
			const std::string text5 = i18n::t("Insert bills");
			const std::string text6 = i18n::t("Press the button when done");
			const std::string text7 = i18n::t("Scan QR code with mobile wallet app");
			const Font text4_font = u8g2_courier_prime_code_9pt;
			int16_t text4_x = numbering1_bbox.x + numbering1_bbox.w + (line_spacing / 2);// left, next to the numbering
			int16_t text4_y = numbering1_bbox.y + (line_spacing / 2);// align w/ first number
			renderText(text4, text4_font, text4_x, text4_y, false);
			int16_t text5_y = numbering2_bbox.y + (line_spacing / 2);// align w/ second number
			renderText(text5, text4_font, text4_x, text5_y, false);
			int16_t text6_y = numbering3_bbox.y + (line_spacing / 2);// align w/ third number
			renderText(text6, text4_font, text4_x, text6_y, false);
			int16_t text7_y = numbering4_bbox.y + (line_spacing / 2);// align w/ fourth number
			renderText(text7, text4_font, text4_x, text7_y, false);
		}
		finishNewScreen("instructions");
	}

	void showInsertFiatScreen(const float &amount) {
		if (!screen_epaper::isReady()) return;
		logger::write("Show screen: Insert Fiat");
		startNewScreen();
		const int16_t margin = 20;
		const int16_t center_x = display.epd2.WIDTH / 2;// center
		BoundingBox prevText_bbox;
		{
			// Render amount + fiat currency symbol (top-center).
			const std::string text = getAmountFiatCurrencyString(amount);
			const int16_t pos_x = center_x;
			const int16_t pos_y = (display.epd2.HEIGHT / 2) - (margin * 3);
			const uint16_t max_w = display.epd2.WIDTH - (margin * 2);
			const Font font = getBestFitFont(text, monospaceFonts, max_w);
			prevText_bbox = renderText(text, font, pos_x, pos_y);
		}
		const float buyLimit = config::getFloat("buyLimit");
		if (buyLimit > 0) {
			std::string text = i18n::t("Limit") + " = ";
			text += util::floatToStringWithPrecision(buyLimit, config::getUnsignedInt("fiatPrecision"));
			text += " " + config::getString("fiatCurrency");
			const int16_t pos_x = center_x;
			const int16_t pos_y = prevText_bbox.y + prevText_bbox.h + margin;
			prevText_bbox = renderText(text, monospaceFontSmall, pos_x, pos_y);
		}
		const float exchangeRate = platform::getExchangeRate();
		if (exchangeRate > 0) {
			std::string text = "1 BTC = ";
			text += util::floatToStringWithPrecision(exchangeRate, config::getUnsignedInt("fiatPrecision"));
			text += " " + config::getString("fiatCurrency");
			const int16_t pos_x = center_x;
			const int16_t pos_y = prevText_bbox.y + prevText_bbox.h + margin;
			prevText_bbox = renderText(text, monospaceFontSmall, pos_x, pos_y);
		}
		{
			// Instructional text #1:
			const std::string text = i18n::t("Insert bills");
			const int16_t pos_x = center_x;
			const int16_t pos_y = prevText_bbox.y + prevText_bbox.h + (margin * 2);
			prevText_bbox = renderText(text, monospaceFontNormal, pos_x, pos_y);
		}
		{
			// Instructional text #2:
			const std::string text = "(" + i18n::t("press button when done") + ")";
			const uint16_t max_w = std::ceil((display.epd2.WIDTH * 4) / 5);
			const Font font = getBestFitFont(text, monospaceFonts, max_w);
			const int16_t pos_x = center_x;
			const int16_t pos_y = prevText_bbox.y + prevText_bbox.h + margin;
			renderText(text, font, pos_x, pos_y);
		}
		finishNewScreen("insertFiat");
	}

	void showTradeCompleteScreen(
		const float &amount,
		const std::string &qrcodeData,
		const std::string &t_referencePhrase
	) {
		if (!screen_epaper::isReady()) return;
		logger::write("Show screen: Trade Complete");
		startNewScreen(0/* always scrub */);
		// Margin between rendered elements.
		const int16_t margin = 20;
		const int16_t line_spacing = 8;
		const uint16_t left_screen_w = display.epd2.WIDTH * 0.8;
		BoundingBox instr_text1_bbox;
		{
			// Render instructional text (bottom-left).
			const std::vector<std::string> lines = splitTextIntoLines(i18n::t("Scan with mobile app to redeem and take a picture for your records"), 2);
			const Font font = getBestFitFont(lines[0], monospaceFonts, left_screen_w);
			instr_text1_bbox = calculateTextSize(lines[0], font);
			BoundingBox instr_text2_bbox = calculateTextSize(lines[1], font);
			const int16_t instr_text2_x = margin;// left
			const int16_t instr_text2_y = display.epd2.HEIGHT - (instr_text2_bbox.h + margin);// bottom
			instr_text2_bbox = renderText(lines[1], font, instr_text2_x, instr_text2_y, false);
			const int16_t instr_text1_x = instr_text2_x;// align w/ other text line
			const int16_t instr_text1_y = instr_text2_bbox.y - (instr_text1_bbox.h + (margin / 2));// above other text line
			instr_text1_bbox = renderText(lines[0], font, instr_text1_x, instr_text1_y, false);
		}
		BoundingBox qrcode_bbox;
		{
			// Render QR code (top-left).
			const int16_t qr_x = margin;// left
			const int16_t qr_y = margin;// top
			const uint16_t qr_max_w = left_screen_w - qr_x;
			const uint16_t qr_max_h = display.epd2.HEIGHT - ((display.epd2.HEIGHT - instr_text1_bbox.y) + margin);
			qrcode_bbox = renderQRCode(qrcodeData, qr_x, qr_y, qr_max_w, qr_max_h, false);
		}
		BoundingBox amount_text_bbox;
		{
			// Render amount + fiat currency symbol (top-right).
			const std::string amount_text = getAmountFiatCurrencyString(amount);
			const uint16_t amount_max_w = display.epd2.WIDTH - (qrcode_bbox.x + qrcode_bbox.w + (margin * 2));
			const Font amount_font = getBestFitFont(amount_text, monospaceFonts, amount_max_w);
			amount_text_bbox = calculateTextSize(amount_text, amount_font);
			const int16_t amount_text_x = display.epd2.WIDTH - (amount_text_bbox.w + margin);// right
			const int16_t amount_text_y = qrcode_bbox.y - line_spacing;// top
			amount_text_bbox = renderText(amount_text, amount_font, amount_text_x, amount_text_y, false);
		}
		{
			// Render reference code (bottom-right).
			const std::string referencePhrase = util::toUpperCase(t_referencePhrase);
			std::vector<std::string> words = util::stringListToStringVector(referencePhrase, ' ');
			const std::string deviceReferencePhrase = util::toUpperCase(config::getString("referencePhrase"));
			if (deviceReferencePhrase != "") {
				const std::vector<std::string> deviceWords = util::stringListToStringVector(deviceReferencePhrase, ' ');
				words.insert(words.end(), deviceWords.begin(), deviceWords.end());
			}
			const Font word_font = monospaceFontSmall;
			BoundingBox prev_word_bbox;
			for (int index = 0; index < words.size(); index++) {
				const std::string word = words.at(index);
				const BoundingBox word_bbox = calculateTextSize(word, word_font);
				const int16_t word_x = display.epd2.WIDTH - (word_bbox.w + margin);// right
				int16_t word_y = prev_word_bbox.y + prev_word_bbox.h + line_spacing;
				if (index == 0) {
					word_y += amount_text_bbox.y + amount_text_bbox.h + line_spacing;
				}
				prev_word_bbox = renderText(word, word_font, word_x, word_y, false);
			}
		}
		finishNewScreen("tradeComplete");
	}
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

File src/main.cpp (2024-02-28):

#include "main.h"

unsigned int buttonDelay;
std::string initializeScreen = "";


void setup() {
	Serial.begin(MONITOR_SPEED);
	spiffs::init();
	config::init();
	logger::init();
	logger::write(firmwareName + ": Firmware version = " + firmwareVersion + ", commit hash = " + firmwareCommitHash);
	logger::write(config::getConfigurationsAsString());
	jsonRpc::init();
	network::init();
	screen::init();
	billAcceptor::init();
	button::init();
	initializeScreen = cache::getString("lastScreen");
	logger::write("Cache loaded lastScreen: " + initializeScreen);
	buttonDelay = config::getUnsignedInt("buttonDelay");
	if (button::isPressedAtStartup()) {
		logger::write("Button pressed during startup, start bluetooth.");
		bluetooth::init();
	}
}

float getAccumulatedValue() {
	float accumulatedValue = billAcceptor::getAccumulatedValue();
	const float billAcceptorEscrowValue = billAcceptor::getEscrowValue();
	if (billAcceptorEscrowValue > 0) {
		const float buyLimit = config::getFloat("buyLimit");
		if (billAcceptorEscrowValue + accumulatedValue > buyLimit) {
			billAcceptor::rejectEscrow();
		} else {
			billAcceptor::acceptEscrow();
		}
	}
	return accumulatedValue;
}

float amountShown = 0;
unsigned long tradeCompleteTime = 0;

void writeTradeCompleteLog(const float &amount, const std::string &signedUrl) {
	std::string msg = "Trade completed:\n";
	msg += "  Amount  = " + util::floatToStringWithPrecision(amount, config::getUnsignedShort("fiatPrecision")) + " " + config::getString("fiatCurrency") + "\n";
	msg += "  URL     = " + signedUrl;
	logger::write(msg);
}

void runAppLoop() {
	screen::loop();
	network::loop();
	platform::loop();
	billAcceptor::loop();
	button::loop();
	const std::string currentScreen = screen::getCurrentScreen();
	if (currentScreen == "" && screen::isReady()) {
		if (config::getBool("enabled")) {
			if (initializeScreen == "insertFiat") {
				const std::string cacheAccumulatedValue = cache::getString("accumulatedValue");
				logger::write("Cache loaded accumulatedValue: " + cacheAccumulatedValue);
				if (cacheAccumulatedValue != "") {
					billAcceptor::setAccumulatedValue(util::stringToFloat(cacheAccumulatedValue));
					screen::showInsertFiatScreen(util::stringToFloat(cacheAccumulatedValue));
					billAcceptor::disinhibit();
				} else {
					screen::showSplashScreen();
					billAcceptor::disinhibit();
				}
			} else if (initializeScreen == "tradeComplete") {
				const std::string cachedQrcodeData = cache::getString("qrcodeData");
				const std::string cachedAccumulatedValue = cache::getString("accumulatedValue");
				const std::string cachedReferencePhrase = cache::getString("referencePhrase");
				logger::write("Cache loaded qrcodeData: " + cachedQrcodeData);
				logger::write("Cache loaded accumulatedValue: " + cachedAccumulatedValue);
				logger::write("Cache loaded referencePhrase: " + cachedReferencePhrase);
				if (cachedQrcodeData != "" && cachedAccumulatedValue != "" && cachedReferencePhrase != "") {
					screen::showTradeCompleteScreen(util::stringToFloat(cachedAccumulatedValue), cachedQrcodeData, cachedReferencePhrase);
					billAcceptor::inhibit();
				} else {
					screen::showSplashScreen();
					billAcceptor::disinhibit();
				}
			} else {
				screen::showSplashScreen();
				billAcceptor::disinhibit();
			}
		} else {
			screen::showDisabledScreen();
			billAcceptor::inhibit();
		}
		initializeScreen = "";
	}
	const float accumulatedValue = getAccumulatedValue();
	const bool tradeInProgress = accumulatedValue > 0 && (currentScreen == "insertFiat" || currentScreen == "tradeComplete");
	if (
		// Do not disable device when a trade is in progress.
		!tradeInProgress &&
		(
			// Device is disabled via configuration option.
			!config::getBool("enabled") ||
			// Online-only mode and not connected to platform.
			config::getBool("onlineOnly") && !platform::isConnected() ||
			// Bill acceptor is not connected.
			(!billAcceptor::isConnected() && millis() > 10000)
		)
	) {
		// Show device disabled screen and do not allow normal operation.
		if (currentScreen != "disabled") {
			billAcceptor::inhibit();
			screen::showDisabledScreen();
		}
	} else {
		// Device is enabled.
		if (currentScreen == "disabled") {
			// Previously disabled, return to normal operation.
			screen::showSplashScreen();
			billAcceptor::disinhibit();
		}
		if (
			accumulatedValue > 0 &&
			currentScreen != "insertFiat" &&
			currentScreen != "tradeComplete"
		) {
			screen::showInsertFiatScreen(accumulatedValue);
			amountShown = accumulatedValue;
		}
		if (currentScreen == "splash") {
			if (button::isPressed()) {
				screen::showInstructionsScreen();
			}
		} else if (currentScreen == "instructions") {
			if (button::isPressed()) {
				screen::showInsertFiatScreen(0);
			}
		} else if (currentScreen == "insertFiat") {
			if (button::isPressed()) {
				if (accumulatedValue > 0) {
					// Button pushed while insert fiat screen shown and accumulated value greater than 0.
					// Generate random words that will be displayed to the user as a human-friendly proof/reference code.
					const std::string referencePhrase = util::generateRandomPhrase(5);
					Lnurl::Query customParams;
					customParams["r"] = referencePhrase;
					const float exchangeRate = platform::getExchangeRate();
					if (exchangeRate > 0) {
						customParams["er"] = std::to_string(exchangeRate);
					}
					// Create a withdraw request and render it as a QR code.
					const std::string signedUrl = util::createSignedLnurlWithdraw(accumulatedValue, customParams);
					const std::string encoded = util::lnurlEncode(signedUrl);
					std::string qrcodeData = "";
					// Allows upper or lower case URI schema prefix via a configuration option.
					// Some wallet apps might not support uppercase URI prefixes.
					qrcodeData += config::getString("uriSchemaPrefix");
					// QR codes with only uppercase letters are less complex (easier to scan).
					qrcodeData += util::toUpperCase(encoded);
					screen::showTradeCompleteScreen(accumulatedValue, qrcodeData, referencePhrase);
					writeTradeCompleteLog(accumulatedValue, signedUrl);
					billAcceptor::inhibit();
					tradeCompleteTime = millis();
				} else {
					// Button pressed with zero amount.
					screen::showInstructionsScreen();
				}
			} else {
				// Button not pressed.
				// Ensure that the amount shown is correct.
				if (amountShown != accumulatedValue) {
					screen::showInsertFiatScreen(accumulatedValue);
					amountShown = accumulatedValue;
				}
			}
		} else if (currentScreen == "tradeComplete") {
			if (button::isPressed() && millis() - tradeCompleteTime > buttonDelay) {
				// Button pushed while showing the transaction complete screen.
				// Reset accumulated values.
				billAcceptor::resetAccumulatedValue();
				billAcceptor::disinhibit();
				amountShown = 0;
				screen::showSplashScreen();
			}
		}
	}
}
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

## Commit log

2020-01-26 docs: getting started with esp32
2020-01-26 docs: tft screen cable mapping
2020-02-22 TFT/ESP32 were flipped for most pins in table
2020-02-23 Refactor, follow flow as described by issue #17
    Display accumulated fiat value
2020-02-24 Ignore extraneous signals on COIN pin
2020-04-15 3D model for Dell PC box
    [dell-pc-case--all.3mf, dell-pc-case--all.scad, dell-pc-case--all.stl]
2020-05-20 prototype case v1
    [bleskomat-prototype-case-v1.dxf]
2020-05-23 Pass device port as arg to monitor command
2020-05-26 esp32-wroom data sheet
2020-05-30 Bleskomat w/ coin acceptor wiring schematic
2020-05-31 Document wiring of hardware device
2020-06-10 parts list spreadsheet
    [parts-list.ods]
2020-06-17 fixup wiring table for tft
2020-06-23 Stencils (logo, bitcoin-lightning)
    [stencil-120-240mm.svg_1mm.3mf, stencil-120mm.svg_1mm.stl, stencil-144mm.svg_1mm.stl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]
2020-06-23 Moved 3d models to assets dir
    [bleskomat-prototype-case-v1.dxf, dell-pc-case--all.3mf, dell-pc-case--all.scad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]
2020-06-24 case measurements
2020-06-25 bitcoin-lightning stencil stl files
    [coin.svg_1mm.stl, lightning.svg_1mm.stl, symbol.svg_1mm.stl]
2020-06-25 bitcoin-lightning stencils fixup
    [symbol.svg_1mm.stl]
2020-07-04 feat: button integration
2020-07-18 docs: case measurements bended - spanish
2020-07-20 Button refactor
    Don't render QR code while still counting coins
    Clear QR code when button pressed (if QR code displayed)
2020-07-29 updated parts list
    [parts-list.ods]
2020-08-04 Coin acceptor with relay module
2020-08-04 Updated parts list (spreadsheet)
    [parts-list.ods]
2020-08-05 Latest wiring diagram
2020-08-05 Updated readme w/ latest wiring diagram
2020-08-05 Changed export name of wiring diagram SVG
2020-08-06 Wiring alignment clean-up
2020-08-07 Fixup readme (wiring instructions)
2020-08-07 Fix pin naming for wiring hx616
2020-08-07 Instructions for wiring the step-down converter
2020-09-26 Updated wiring diagram
2020-09-26 Updated TFT cable mappings, ESP32 common ground note, power warnings
2020-09-26 Removed unnecessary extra wiring diagram
2020-09-28 Print full error stack trace, wait for db ready
2020-09-28 Moved parts list to business repo
    [parts-list.ods]
2020-11-14 Can now override USB device path
2020-11-15 Load config from SD card
    Wiring of SD card explained in readme
    Generate bleskomat.conf file with `npm run print:config` task
2020-11-24 Write logs to file on SD card
    Removed instances of printf()
    Cleaned-up logger::write() usage
2020-12-04 Use e-paper display module instead of TFT
    SD card SPI module added
    Splash screen (BLESKOMAT + slogan)
    Instructions screen
    Insert fiat screen (amount + symbol)
    Transaction complete screen (QR code + instruction)
    Added custom fonts, script and instructions to build more
2020-12-24 Refactor button module
    Left button::pushed() for backwards compatibility (temporary)
    Calling pushed() multiple times in same loop will give same result
2020-12-24 Firmware version number, commit hash now printed to serial monitor and debug log file
2020-12-28 docs: change case designes in svg
2020-12-30 Fix writing to serial monitor due to bill acceptor module
    [main.cpp]
2021-01-02 Removed button::pushed() function and usage
2021-01-03 Fix render amount text by stepping down font size
    [epaper.cpp]
2021-01-03 Add "push button to start" text to splash screen
2021-01-03 Show transactionLimit on insertFiat screen
2021-01-03 Disallow inserting coins if possible to exceed tx limit
2021-01-14 fix: change transactionLimit to buyLimit (#85)
    * fix: change transactionLimit to buyLimit
    * Only turn off coin acceptor when buyLimit > 0 and not already off
    [epaper.cpp, main.cpp]
2021-01-17 Removed out-dated wiring diagram from readme
    Added note that it needs to be updated with latest components.
2021-01-18 feat: disable bill acceptor (#69)
    * feat: disable bill acceptor
    * fix: change bill acceptor pins so it works
    [bill-acceptor.cpp, main.cpp]
2021-01-26 feat: pcb v0.1
    [bleskomat-board-B_Cu.gbl, bleskomat-board-B_Mask.gbs, bleskomat-board-B_SilkS.gbo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]
2021-03-08 ESP programmer docs, esp32 pinout image
2021-03-17 feat: pcb test for assembly
    [test-board-esp32-assembly-B_Cu.gbr, test-board-esp32-assembly-B_Mask.gbr, test-board-esp32-assembly-B_Paste.gbr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]
2021-03-17 feat: pcb v2.1.0
    [bleskomat-board-B_Cu.gbl, bleskomat-board-B_Mask.gbs, bleskomat-board-B_SilkS.gbo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]
2021-04-09 pcb: add centroid pick and place file
    [bleskomat-v2.1.0.kicad_pcb]
2021-04-19 feat: pcb boot and flash circuits
2021-04-26 Display 7 words on transaction complete screen
    New optional config referencePhrase is device 2-word unique identifier
2021-04-26 Fix precision of buyLimit on insert fiat screen
    Re-align insert fiat screen
    [epaper.cpp]
2021-05-06 Websockets instead of HTTP polling for device options
    Can receive device options, exchangeRate from server
    Authorization challenge signature (HMAC-SHA256) when initializing socket
2021-05-24 Move assets/docs to more appropriate repos
    Added fonts that are used in the firmware
    General clean-up
    [bleskomat-prototype-case-v1.dxf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]
2021-05-24 If set, show exchange rate on insert fiat screen
2021-06-02 Disable device when platform offline
2021-06-11 Added button wiring instructions
2021-06-14 Fix issue 130 - QR code scanning problem
    [epaper.cpp, main.cpp]
2021-06-15 Fix issue 59: SD card read/write errors when epaper SPI connected
    [epaper.cpp, logger.cpp, main.cpp]
2021-06-25 New strictTls config (default false)
    Remove platformCACert, pingCACert configs - use files on SD card instead
    Reduce RAM usage by using const where possible
    Improve platform down check
    Re-try SD card mount in case of failures
    Don't disable when trade in-progress
    renderText and renderQRCode now return bounding bbox
    [epaper.cpp, logger.cpp, main.cpp]
2021-06-25 fix: when disable screen acceptors should disable (#133)
    * fix: when disable screen acceptors should disable
    * Move new disable/enableAcceptors methods to modules
    [main.cpp]
2021-07-04 Clarify build flag, pin naming for bill/coin acceptors
2021-07-23 Fix QR code margin problem when display inside case
    [epaper.cpp]
2021-10-23 fix: mounting sdcard after change screen (#141)
    * fix: mounting sdcard after change screen
    * The SD card should be automatically re-mounted at loop
    There was a logic error in the if statement
2022-05-02 Firmware version build flag, var
    Print apiKey.key config key, but XXX instead of value
2022-05-24 Use fixed version numbers: platform, framework
2022-05-27 Use SPIFFS to save log files
    Improved logging
    Button delay: Remove delay(), use elapsed time check instead
2022-05-29 Improve logging and error handling in JSON-RPC
    [json-rpc.cpp]
2022-05-30 Fixup online mode
    Removed ping-server code
    Simplified platform code
    Fix TLS CA cert usage
    [json-rpc.cpp, logger.cpp, main.cpp]
2022-05-31 Bill: Cleaner logging, handle case where note rejected
    Enable escrow timeout
2022-05-31 Default buttonDelay = 10 seconds
2023-02-09 fix(bill-acceptor): wait for escrow mode confirmation (#150)
    * fix(bill-acceptor): wait for escrow mode confirmation
    * Debounce enable escrow commands
    ---------
    [bill-acceptor.cpp]
2023-02-09 Fix debounce of enable escrow command
    [bill-acceptor.cpp]
2023-04-29 Remove opensans font
    Fixup font rendering on all screens
    [epaper.cpp]
2024-02-28 Feat: bluetooth with jsonrpc (#162)
    * feat: add bluetooth functionality
    * feat: update json-rpc to receive bluetooth messages
    * feat: add ble initialization
    * feat: start bluetooth only when button is pressed at start up
    * feat: bluetooth full support JSON RPC send and receive
    * feat(config): expose isConfigKey
    * fix(json-rpc): removed non-existing method definition
    * fixup! feat: bluetooth full support JSON RPC send and receive
    * feat(json-rpc): extend getconfig api to allow partials
    * Added waiting to connect screen
    * feat: when waitingToConnect screen inhibit billAcceptor
    Co-autho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
    [epaper.cpp]
2024-06-05 fix: when params is empty array returns full config (#163)
    * fix: when params is empty array returns full config
    * Fix minor syntax error
    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
    [json-rpc.cpp]

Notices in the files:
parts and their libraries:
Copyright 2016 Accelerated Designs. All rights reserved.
